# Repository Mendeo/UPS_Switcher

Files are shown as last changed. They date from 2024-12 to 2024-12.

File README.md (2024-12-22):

# Автоматическое выключение и включение домашнего сервера при перебоях с электричеством

Устройство, которое в момент отключения внешнего электричества подаёт сигнал на компьютер, чтобы тот выключился, ожидает его выключения и механически отключает источник бесперебойного питания (ИБП), к которому этот компьютер подключён. После возобновления электроснабжения - снова механически включает бесперебойник.

Состояние электросети отслеживает микроконтроллер в виде Arduino Pro Mini. Когда электричество отключают, то ардуино подаёт сигнал на GPIO контакт. Если в роли компьютера выступает компьютер с GPIO, например Raspberry Pi, то он сразу получает сигнал на выключение. Если это обычный компьютер (без GPIO), то требуется ещё один промежуточный контроллер в виде Arduino Nano, который принимает сигнал от GPIO, а с компьютером связан через USB. Для включения и выключения бесперебойника используется сервомашинка, которая нажимает на кнопку на ИБП. Если электричество вернут в процессе отключения компьютера, то кнопка нажимается дважды, чтобы снова включить компьютер. Ожидая появления электричества, устройство работает от батареек. Скетч для прошивки Arduino Pro Mini - контроллера основного устройства находится в файле [controller/controller.ino](controller/controller.ino). А скетч для Arduino Nano (промежуточный контроллер для компьютеров без GPIO) в файле [comp/serial/controller/controller.ino](comp/serial/controller/controller.ino).

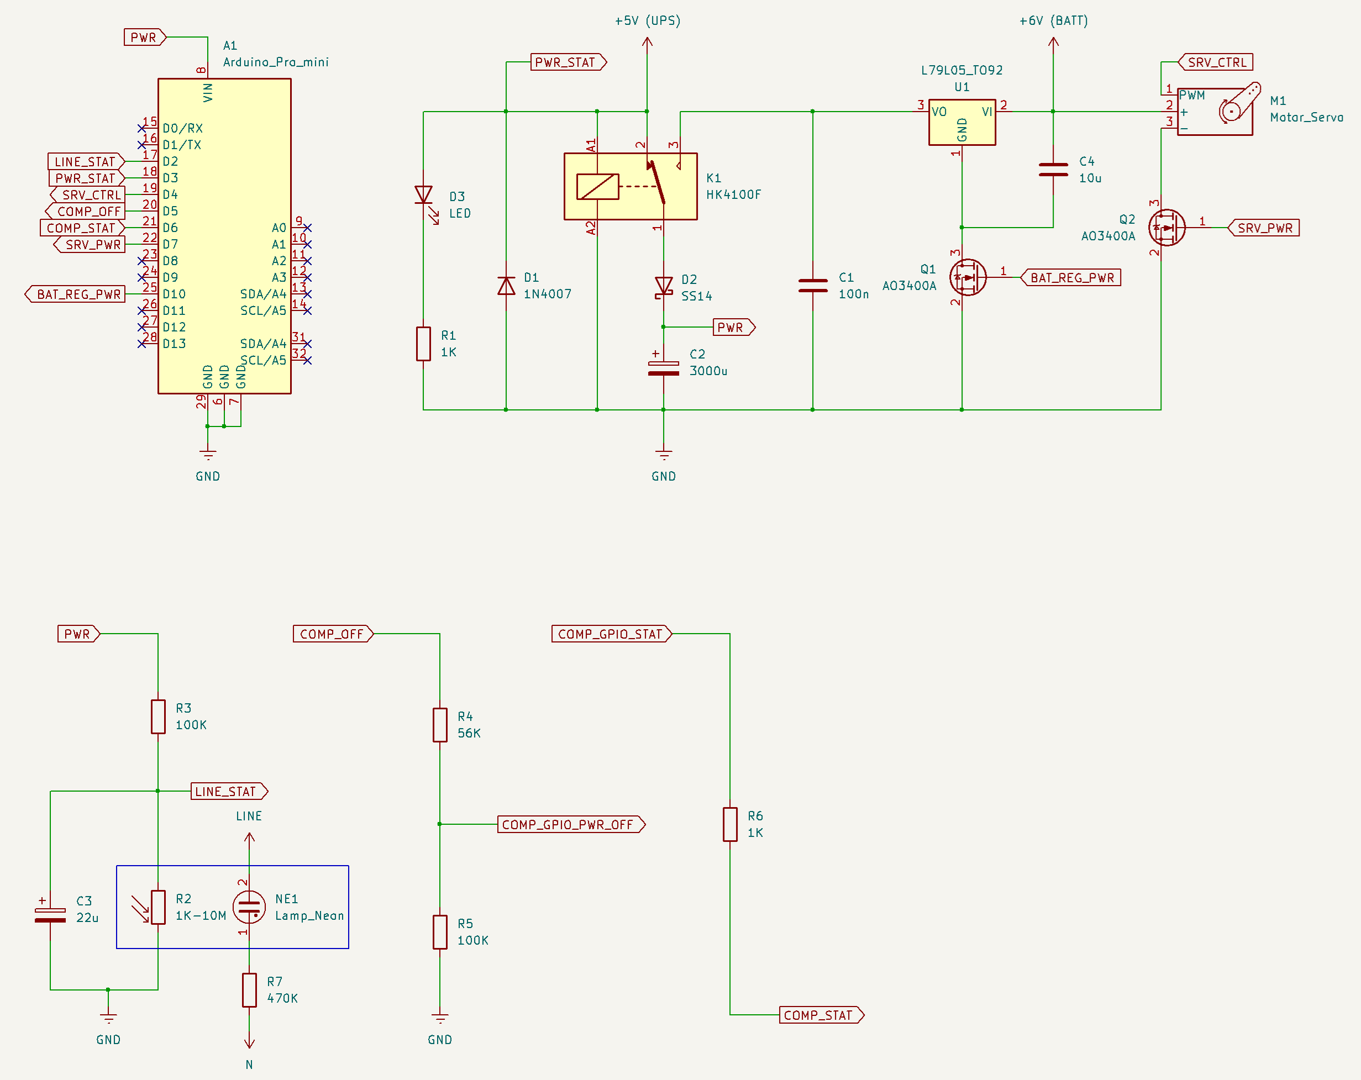
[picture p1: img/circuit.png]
Электрическая схема устройства


Для переключения источника питания устройства применяется пятивольтовое реле. На схеме используется HK4100F, катушка которого потребляет примерно 40 мА. Диод D1 служит для защиты от обратного тока при переключении катушки. При подаче питания на катушку устройство питается от внешнего источника. Катушка сразу подключена к внешнему питанию, поэтому как только оно появляется, то прибор сразу переходит на него.

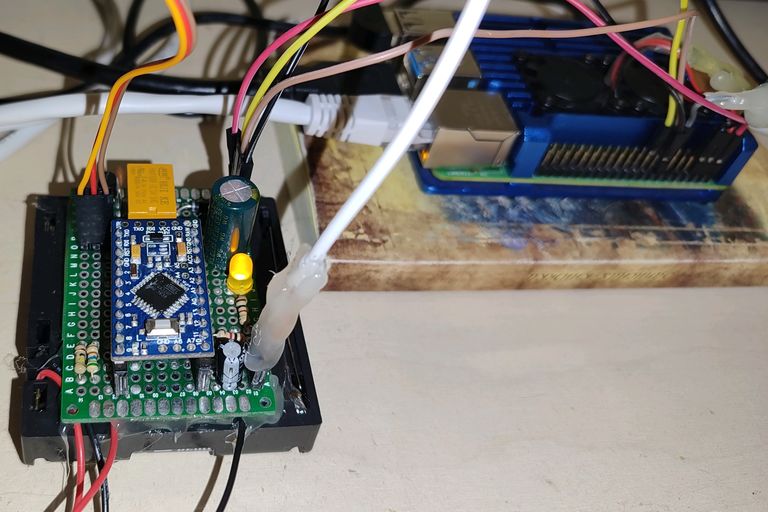
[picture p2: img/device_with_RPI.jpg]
Внешний вид устройства


При отключении питания катушка отключается и реле переключает питание на батарейное. Я использую 4 батарейки AA, что в сумме даёт напряжение 6В, поэтому требуется уменьшить его до 5 вольт. Для этого используется линейный 5В преобразователь L79L05 в корпусе TO92. Этот преобразователь в холостом режиме потребляет примерно 2,5 мА, поэтому будет сажать батарейки даже если устройство питается от внешнего питания. Чтобы этого не было, предусмотрен транзистор Q1, который полностью размыкает цепь связанную с батарейками, когда они не должны использоваться и открывается при переходе на батарейное питание при помощи сигнала от ардуино. О наличии внешнего питания ардуино судит по сигналу PWR_STAT.
Ещё для экономии батареек с Arduino Pro Mini удалены светодиод, который горит при наличии питания и преобразователь напряжения, который в данном проекте не используется, но потребляет ток. Каждый раз при переключении на батарейки микроконтроллер проверяет напряжение питания. И если оно будет ниже допустимого, то выдаст сообщение об ошибке путём моргания оставшегося светодиода (13-й пин). Проверка напряжения реализована путём переключения АЦП микроконтроллера на измерение внутреннего опорного напряжение 1,1 вольта. При этом опорное напряжение самого АЦП остаётся как обычно - напряжение питания. Поэтому результат измерения 1,1 вольта будет зависеть от напряжения питания.

Чтобы ардуинка не выключалась в момент переключения питания предусмотрен конденсатор C2 ёмкостью 3000 мкФ. Но одного конденсатора недостаточно, т.к. из схемы видно, что при отключении внешнего питания, катушка реле продолжит питаться уже от конденсатора и питание быстро не переключится. Чтобы этого избежать установлен диод Шоттки. Он съедает примерно 0,2 вольта входного напряжения, поэтому на ардуино приходит примерно 4,8 вольта.

Сервомашинка питается только от батареек. Чтобы электроника сервомашинки не сажала батарейки в простое, предусмотрен транзистор Q2, который открывается ардуиной только на время её работы. В проекте используется самая распространённая 9-граммовая серва. Она просто приклеивается к ИБП на толстый двухсторонний скотч. Для работы с сервой используется стандартная для ардуино библиотека [Servo](https://reference.arduino.cc/reference/en/libraries/servo/). Для настройки угла поворота, достаточного для нажимания кнопки, я сделал небольшую тестовую прошивку, которую можно залить в удобную для тестрования ардуино (Arduino UNO).

```c++
#define LED 13
#define SERVO_CONTROL 4
#include <Servo.h>

Servo _srv;

void setup()
{
  pinMode(LED, OUTPUT);
  pinMode(SERVO_CONTROL, OUTPUT);
  _srv.attach(SERVO_CONTROL);
  Serial.begin(9600);
  _srv.write(0);
}

int _angle = 0;

void loop()
{
  if (Serial.available())
  {
    _angle = Serial.readString().toInt();
    Serial.println(_angle);
    _srv.write(_angle);
    delay(500);
    _srv.write(0);
  }
}
```

В сериал мониторе нужно вводить градус поворота. Сервомашинка будет на этот угол поворачиваться, а затем возвращаться в нулевое положение. Нужно добиться, чтобы кнопка успешно нажималась и отжималась и сделать на градус два больше для запаса.

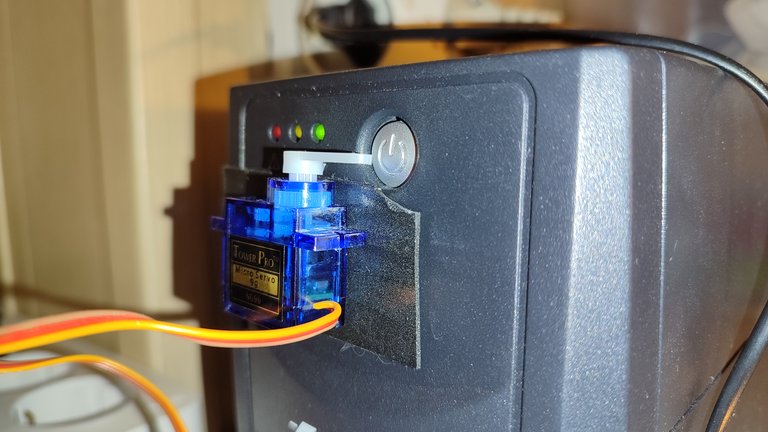
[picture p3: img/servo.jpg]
Сервомашинка, приклеенная к ИБП


Ардуино общается с компьютером или промежуточной Arduino Nano при помощи GPIO. Всего используется два GPIO контакта: COMP_OFF и COMP_STAT.
* COMP_OFF - выходной сигнал Arduino Pro Mini (5-й pin). При высоком уровне на нём компьютер получает сигнал о необходимости выключится. Т.к. мини ПК с GPIO, например, Raspberry Pi использует 3-х вольтовую логику, то COMP_OFF преобразуется во входной сигнал COMP_GPIO_PWR_OFF для Raspberry Pi напряжением чуть меньше 3,3 вольта. Для этого используется делитель, в верхнем плече которого резистор на 56 кОм, а в нижнем - на 100 кОм.
* COMP_STAT - это входной сигнал Arduino Pro Mini (6-й pin) с внутренней подтяжкой к высокому уровню. Когда компьютер включается, он должен установить на этот контакт низкий уровень. Так устройство поймёт, что компьютер работает. COMP_STAT переходит в выходной для GPIO компьютера или промежуточной Arduino Nano контакт COMP_GPIO_STAT. На всякий случай связь сделана через резистор в 1 кОм.

Прибор должен получать информацию о наличии напряжения в розетке. Для этого собирается индикатор напряжения в сети в виде обычной неоновой лампочки NE-2 и фоторезистора. Лампочка питается от сети через резистор 470 кОм. Лампочка и фоторезистор помещаются в пластиковый корпус, изготовленный на 3D принтере. Их выводы помещаются в отдельные корпуса, которые служат для изоляции выводов. Ещё две детали служат для помещения в них подводящих проводов: 230В - к лампе и от прибора к фоторезистору. После сборки отдельные части склеиваются цианокрилатным клеем с содой. Я печатал PETG пластиком. Модели отдельных частей, а также исходный код для среды OpenScad лежат в папке [lineDetector](lineDetector)

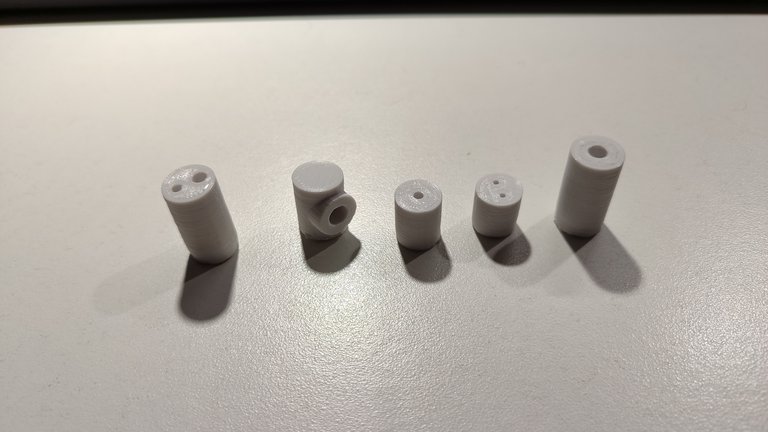
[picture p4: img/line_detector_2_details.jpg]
Детали корпуса индикатора напряжения в сети второй версии


Все оголённые выводы я дополнительно поместил в термоусадку:

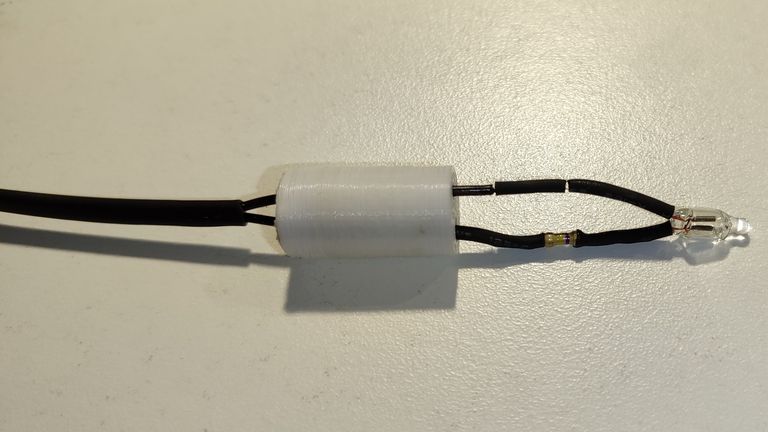
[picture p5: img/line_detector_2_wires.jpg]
Все оголённые выводы дополнительно в термоусадке


Детектор в сборе:

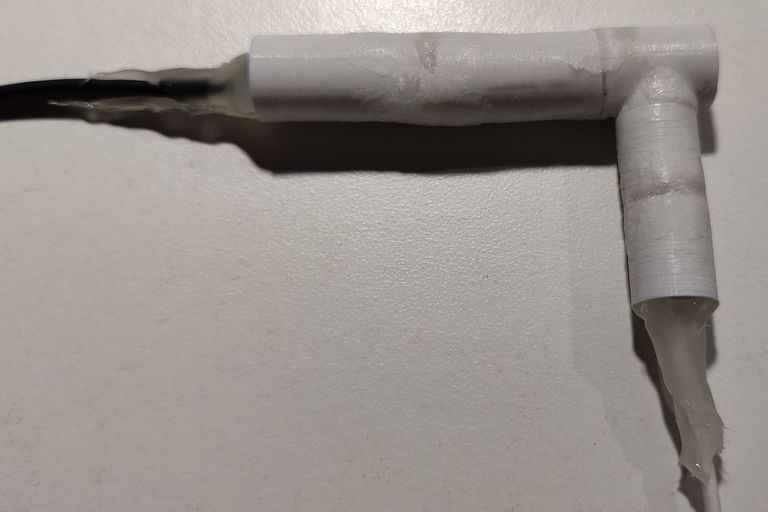
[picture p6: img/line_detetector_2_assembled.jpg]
Индикатор напряжения в сети в распечатанном корпусе


Но какой бы толщины не были стенки, пластик всё равно пропускает свет. Поэтому, чтобы всё работало, нужно обернуть полученное изделие в фольгу. Для этого идеально подходит алюминиевый скотч.

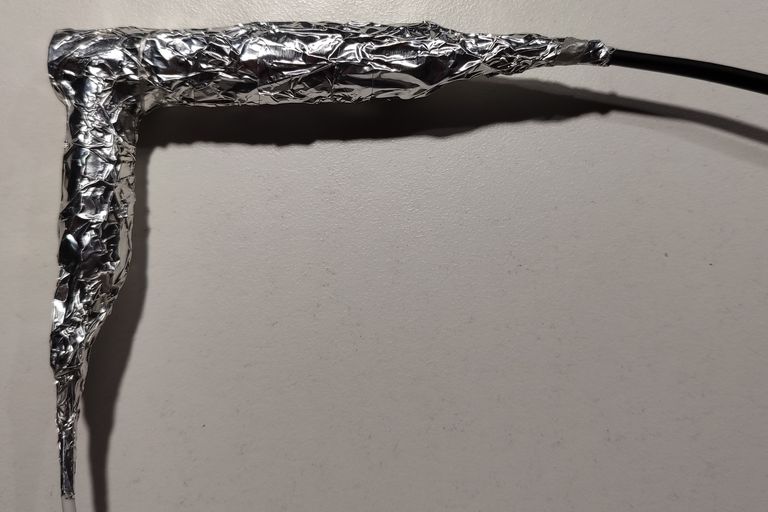
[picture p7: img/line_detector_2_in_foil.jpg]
Индикатор напряжения в сети в распечатанном корпусе и в фольге


В моём случае фоторезистор в полной темноте имеет сопротивление больше 200 МОм, а при освещение неоновой лампочкой - сопростивление падает примерно до 2 кОм. Сигнал LINE_STAT формируется из делителя напряжения, где фоторезистор входит в нижнее плечо. Верхнее плечо - резистор на 100 кОм. В этом случае сигнал LINE_STAT является инверсным: когда электричество есть на нём уровень около нуля, а при отключении сети: почти 5 вольт. Для того, чтобы убрать пульсации и случайные срабатывания ставится конденсатор C3. На схеме указан конденсатор на 22 мкФ. В этом случае детектор срабатывает аж почти через две секунды после отключения электричества в сети. Можно варьировать как удобно.

Программная часть для компьютера написана на языке Tcl. Для компьютеров с GPIO (Raspberry Pi) используется файл [comp/rpi_gpio/watcher.tcl](comp/rpi_gpio/watcher.tcl). В коде задан входным контактом 27-ой пин, выходным - 22-й пин. Управление GPIO в этом коде осуществляется через библиотеку [libgpiod](https://git.kernel.org/pub/scm/libs/libgpiod/libgpiod.git/about/). А именно, используются готовые утилиты для работы с GPIO. Для отслеживания входных сигналов применяется утилита gpiomon, а для установки выходных сигналов - gpioset. Одним из преимуществ такого подхода в управлении GPIO является то, что скрипт watcher.tcl имеет монопольный доступ к GPIO и пока его процесс не завершён, никакой другой процесс не может иметь доступа к используемым watcher.tcl GPIO контактактам, что положительно сказывается на безопасности. Библиотека libgpiod уже предустановлена в последних версиях Raspbian OS, но если нет, то её можно установить.

```
sudo apt install gpiod
```

Для автозагрузки watcher.tcl используется юнит Systemd:

```
[Unit]
Description=Service for communication with the UPS control device

[Service]
User=root
Type=simple
ExecStart=/usr/bin/tclsh /path/to/watcher.tcl

[Install]
WantedBy=multi-user.target
```

Для компьютеров без GPIO, использующих для связи с основным устройством дополнительную Arduino Nano исходный код расположен в файле [comp/serial/comp/watcher.tcl](comp/serial/comp/watcher.tcl). Эта программа в качестве параметра принимает путь к последовательному порту, к которому подключено Arduino Nano (обычно /dev/ttyUSB0). Этот путь следует добавить к ExecStart в юните выше. Алгоритм прост: Arduino Nano всё время шлёт "a\r\n". Когда watcher.tcl запускается и получает с последовательного порта эту команду, то она отсылает "+". Ардуино перестаёт слать "a\r\n" и уходит в глубокий сон (почти перестаёт потреблять энергию). Когда настаёт время выключить сервер, то ардуино просыпается и всё время шлёт "-\r\n".

Если используется Raspberry Pi, то устройство питается от выводов 5 вольт и земля самого одноплатника, т.к. на эти пины питания поступает напряжение даже если Raspberry Pi выключено. В случае обычного компьютера или мини ПК требуется организовать отдельное питание устройства от блока питания, подключённого к ИБП. В моём случае, например, я использовал блок питания самого компьютера с дополнительными выводами, и плату понижения напряжения для преобразования 12 вольт в 5 вольт.

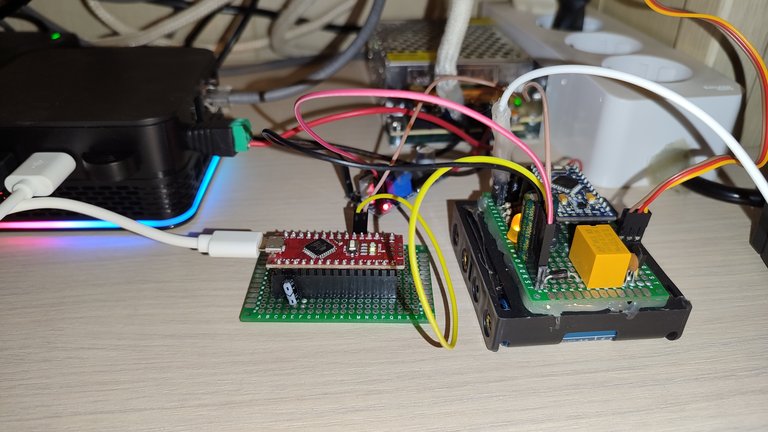
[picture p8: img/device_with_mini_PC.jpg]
Мини ПК с Ардуино вместо GPIO


Итак, для начала работы устройства, нажимаем кнопку reset на ардуино. Если всё нормально, то сначала сервомашинка издаст звук, означающий что устройство включилось и что качалка установлена на нулевой угол. Также, загорится светодиод - обозначающий, что ардуина включилась и пока ещё не ушла в сон. И через некоторое время он погаснет, обозначая, что микроконтроллер ушёл в глубокий сон. Всё. Мониторинг электросети включён. Если же после нажатия reset светодиод начал моргать, то значит нужно искать ошибку. При включении, микроконтроллер проверяет основные сигналы. В случае обнаружения ошибки, ардуино сообщит об этом путём мигания светодиода. Прежде всего устройство должно питаться от основного питания (не батарейки). В противном случае светодиод будет моргать раз в секунду. Эта же ошибка возникнет при сбоях при переключении бесперебойника, если он не включится или не выключится. Далее, проверяется наличие сетевого напряжения. В случае его отсутствия светодиод замигает 10 раз в секунду. Если всё нормально, устройство будет ждать включения сервера (пока не будет притянут к земле соответствующий контакт). Если в течении 3-х минут этого не произойдёт, то светодиод начнёт мигать 2 раза в секунду. И наконец, последняя ошибка - это низкий уровень батареек. Он проверяется при переключении на батарейное питание. В этом случае диод будет мигать 1 раз в 5 секунд. Во всех случаях мигание будет продолжаться 10 минут, потом ардуино уйдёт в сон.

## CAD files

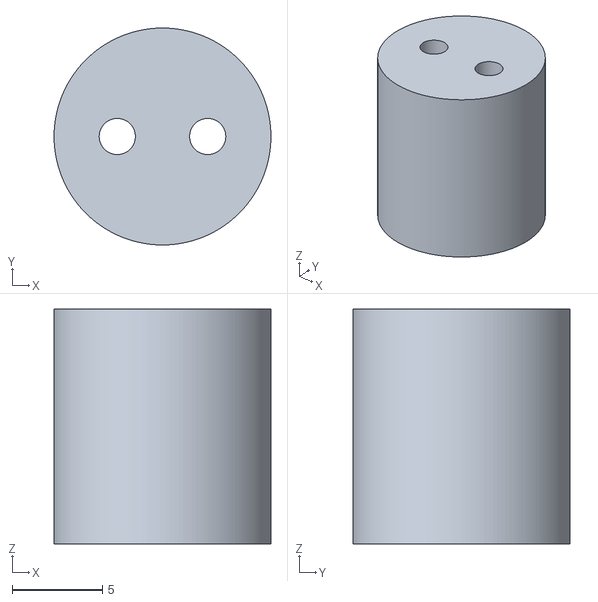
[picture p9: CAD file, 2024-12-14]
lineDetector/resistorPart2.stl
12.0 x 12.0 x 13.0

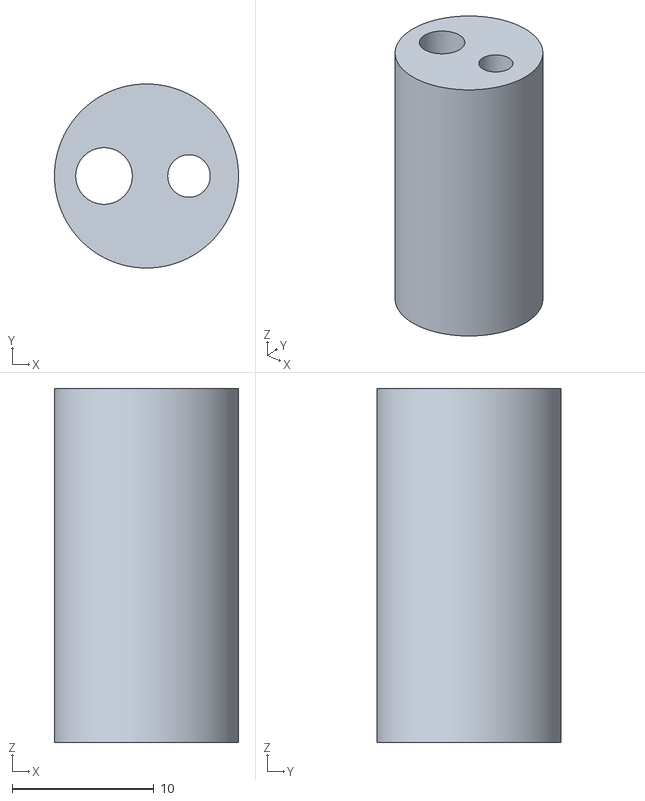
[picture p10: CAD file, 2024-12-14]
lineDetector/lampPart2.stl
13.0 x 13.0 x 25.0

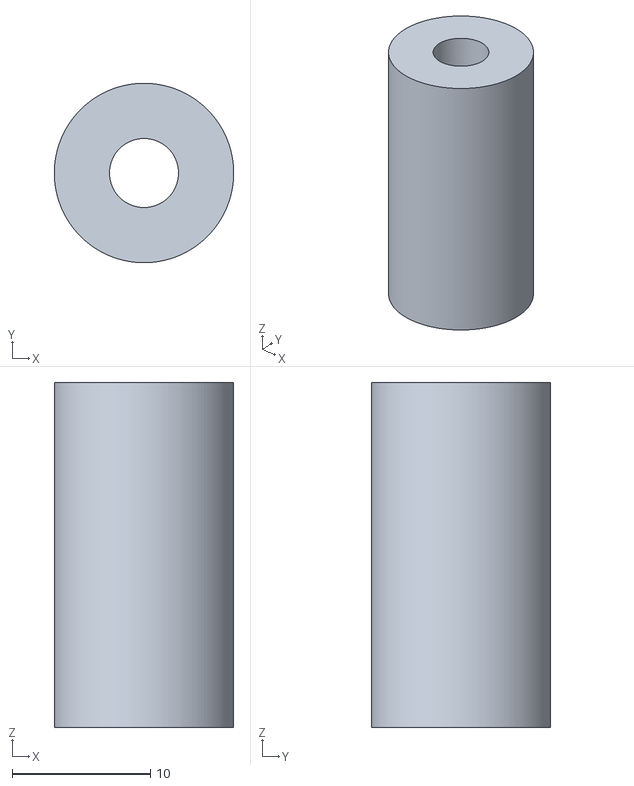
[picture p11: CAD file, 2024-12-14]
lineDetector/lampPart3.stl
13.0 x 13.0 x 25.0

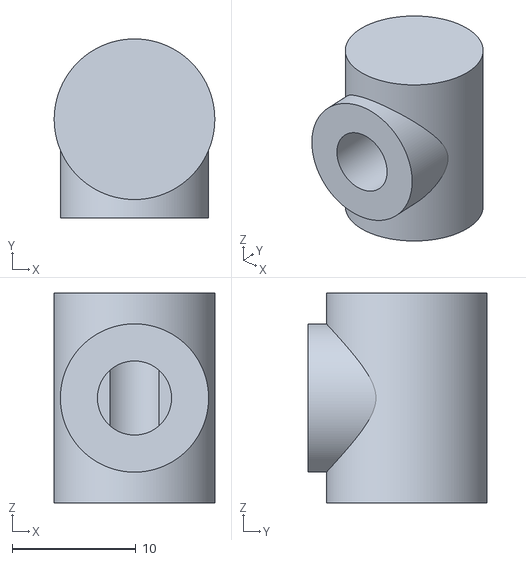
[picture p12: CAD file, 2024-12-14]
lineDetector/lampResistorPart1.stl
13.0 x 14.5 x 17.0

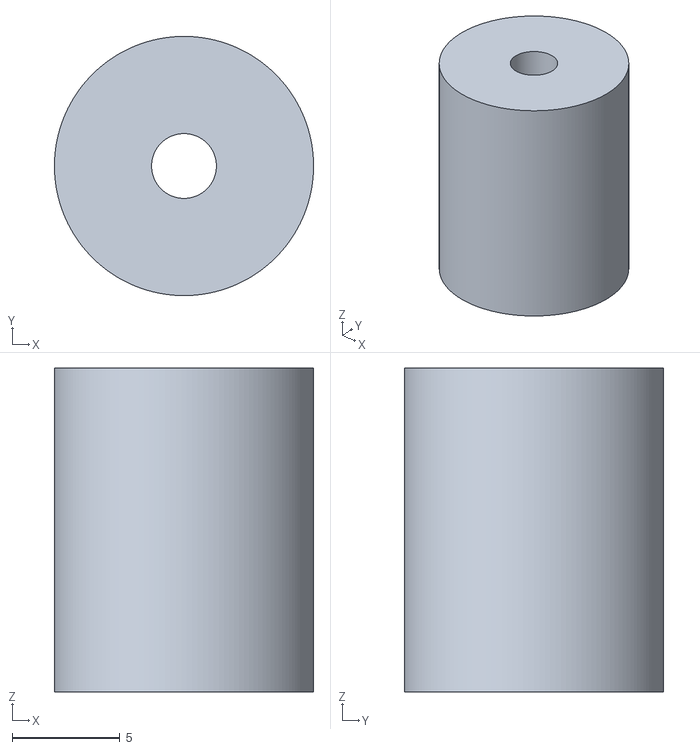
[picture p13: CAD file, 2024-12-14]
lineDetector/resistorPart3.stl
12.0 x 12.0 x 15.0

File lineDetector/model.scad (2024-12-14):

$fn = 150;

lampD = 13;
resistorD = 12;
resistorPart1H = 8;
resistorPart2H = 13;
resistorPart3H = 15;
lampPart1H = 17;
lampPart2H = 25;
lampPart3H = 25;
wireResistorD = 2;
wireLampD = 3;
wireLampWithResistorD = 4;
wireDeltaResistor = 5;
wireDeltaLamp = 6;
wallTLamp = 4;
wallTResistor = 3;
lampCabelD = 5;
resistorCabelD = 3;

/*Отдельно для печати*/
//lampResistorPart1();
lampPart2();
//lampPart3();
//resistorPart2();
//resistorPart3();

/*Общий вид в сборе*/
/*
lampResistorPart1();
%translate([0, 0, -lampPart2H])
lampPart2();
translate([0, 0, -lampPart2H - lampPart3H])
lampPart3();

%translate([0, -resistorPart1H, lampPart1H / 2])
rotate([90, 0, 0])
resistorPart2();
translate([0, -resistorPart1H - resistorPart2H, lampPart1H / 2])
rotate([90, 0, 0])
resistorPart3();
*/

module lampResistorPart1()
{
	translate([0, 0, lampPart1H - wallTLamp])
	cylinder(h = wallTLamp, d = lampD);
	difference()
	{
		union()
		{
			cylinder(h = lampPart1H, d = lampD);
			translate([0, -(lampD / 2 - wallTLamp), lampPart1H / 2])
			rotate([90, 0, 0])
			cylinder(h = resistorPart1H - (lampD / 2 - wallTLamp), d = resistorD);
		}
		translate([0, 0, -1])
		cylinder(h = lampPart1H + 2, d = lampD - 2 * wallTLamp);
		translate([0, -(lampD / 2 - wallTLamp) + 1, lampPart1H / 2])
		rotate([90, 0, 0])
		cylinder(h = resistorPart1H + 1, d = resistorD - 2 * wallTResistor);
	}
}

module resistorPart2()
{
	difference()
	{
		cylinder(h = resistorPart2H, d = resistorD);
		translate([0, 0, -1])
		{
			translate([wireDeltaResistor / 2, 0, 0])
			cylinder(h = lampPart2H + 2, d = wireResistorD);
			translate([-wireDeltaResistor / 2, 0, 0])
			cylinder(h = lampPart2H + 2, d = wireResistorD);
		}
	}
}

module resistorPart3()
{
	difference()
	{
		cylinder(h = resistorPart3H, d = resistorD);
		translate([0, 0, -1])
		cylinder(h = resistorPart3H + 2, d = resistorCabelD);
	}
}

module lampPart2()
{
	difference()
	{
		cylinder(h = lampPart2H, d = lampD);
		translate([0, 0, -1])
		{
			translate([wireDeltaLamp / 2, 0, 0])
			cylinder(h = lampPart2H + 2, d = wireLampD);
			translate([-wireDeltaLamp / 2, 0, 0])
			cylinder(h = lampPart2H + 2, d = wireLampWithResistorD);
		}
	}
}

module lampPart3()
{
	difference()
	{
		cylinder(h = lampPart3H, d = lampD);
		translate([0, 0, -1])
		cylinder(h = lampPart3H + 2, d = lampCabelD);
	}
}

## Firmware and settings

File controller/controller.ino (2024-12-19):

#include <LowPower.h>
#include <Servo.h>

/*
  Сигнал COMP_STATUS инверсный
*/

#define INTERNAL_REF_REAL_VOLTAGE 1.1
#define SERVO_ANGLE 33
#define SERVO_PUSH_TIME 400 //Время на нажатие, зависит от угла.

#define LED 13
#define LINE_STATUS 2
#define BAT_5V_REGULATOR 10
#define SERVO_POWER 7
#define SERVO_CONTROL 4
#define COMP_POWER_OFF_COMMAND 5
#define COMP_STATUS 6
#define MAIN_POWER_STATUS 3

#define COMP_NOT_READY_ERROR 500
#define LOW_BATTERY_ERROR 5000
#define SWITCHING_POWER_ERROR 1000
#define LINE_IS_DOWN_ERROR 100

#define WAIT_COMP_AFTER_START_TIME 180000
#define TIME_FOR_COMP_POWEROFF_AFTER_LINE_DOWN 30000
#define TIME_FOR_UPS_POWEROFF_AFTER_COMP 43000
#define TIME_BEFORE_COMP_POWERON 20000
#define TIME_BEFORE_DEEP_SLEEP 10000

#define BLINK_ERROR_TIME 600000

unsigned long _eventTime = 0;
bool _compIsOn = true;
bool _isMainPower = true;
Servo _srv;
bool _lineIsOk = true;
bool _needSleep = false;
volatile bool _needCheckLine = true;

void setup()
{
  pinMode(LINE_STATUS, INPUT);
  pinMode(MAIN_POWER_STATUS, INPUT);
  pinMode(COMP_STATUS, INPUT_PULLUP);

  pinMode(LED, OUTPUT);
  pinMode(SERVO_POWER, OUTPUT);
  pinMode(COMP_POWER_OFF_COMMAND, OUTPUT);
  pinMode(BAT_5V_REGULATOR, OUTPUT);

  digitalWrite(LED, HIGH);
  digitalWrite(BAT_5V_REGULATOR, HIGH);

  rotateServo(0);
  compPowerOn();
  if (!digitalRead(MAIN_POWER_STATUS)) blink(SWITCHING_POWER_ERROR);
  digitalWrite(BAT_5V_REGULATOR, LOW);
  prepareADCForVCCmeasuring();
  delay(3000); //На зарядку конденсатора перед первой проверкой линии
  checkLine();
  if (!_lineIsOk) blink(LINE_IS_DOWN_ERROR);

  unsigned long timer = millis();
  while (digitalRead(COMP_STATUS))
  {
    if (millis() - timer >= WAIT_COMP_AFTER_START_TIME)
    {
      blink(COMP_NOT_READY_ERROR);
    }
  }
}

void onLineChange()
{
  _needCheckLine = true;
}

void loop()
{
  if (_isMainPower && _compIsOn && _lineIsOk && (millis() - _eventTime) >= TIME_BEFORE_DEEP_SLEEP && !_needCheckLine)
  {
    _needSleep = true;
  }
  else if (_isMainPower && _compIsOn && !_lineIsOk && (millis() - _eventTime) >= TIME_FOR_COMP_POWEROFF_AFTER_LINE_DOWN  && !_needCheckLine)
  {
    compPowerOff();
    waitForCompPowerOff();
    _eventTime = millis();
  }
  else if (_isMainPower && !_compIsOn && !_lineIsOk && (millis() - _eventTime) >= TIME_FOR_UPS_POWEROFF_AFTER_COMP && !_needCheckLine)
  {
    switchUPS();
    _needSleep = true;
  }
  else if (!_isMainPower && !_compIsOn && _lineIsOk && (millis() - _eventTime) >= TIME_BEFORE_COMP_POWERON && !_needCheckLine)
  {
    switchUPS();
    waitForCompPowerOn();
    _needSleep = true;
  }
  else if (!_isMainPower && !_compIsOn && !_lineIsOk && (millis() - _eventTime) >= TIME_BEFORE_DEEP_SLEEP && !_needCheckLine)
  {
    _needSleep = true;
  }
  else if (_isMainPower && !_compIsOn && _lineIsOk && (millis() - _eventTime) >= TIME_BEFORE_COMP_POWERON && !_needCheckLine)
  {
    switchUPS();
    delay(3000);
    switchUPS();
    waitForCompPowerOn();
    _needSleep = true;
  }
  else if (!_isMainPower && _compIsOn && !_needCheckLine)
  {
    _compIsOn = false;
  }
  checkLine();
  if (_needSleep)
  {
    _needSleep = false;
    sleep();
  }
}

void compPowerOff()
{
  digitalWrite(COMP_POWER_OFF_COMMAND, HIGH);
}

void compPowerOn()
{
  digitalWrite(COMP_POWER_OFF_COMMAND, LOW);
}

void rotateServo(int angle)
{
  pinMode(SERVO_CONTROL, OUTPUT);
  digitalWrite(SERVO_POWER, HIGH);
  delay(3);
  _srv.attach(SERVO_CONTROL);
  _srv.write(angle);
  delay(SERVO_PUSH_TIME);
  if (angle > 0)
  {
    _srv.write(0);
    delay(SERVO_PUSH_TIME);
  }
  _srv.detach();
  digitalWrite(SERVO_POWER, LOW);
  pinMode(SERVO_CONTROL, INPUT);
}

void switchUPS()
{
  _isMainPower = digitalRead(MAIN_POWER_STATUS);
  if (_isMainPower) digitalWrite(BAT_5V_REGULATOR, HIGH);
  rotateServo(SERVO_ANGLE);
  unsigned long time = millis();
  while (_isMainPower == digitalRead(MAIN_POWER_STATUS))
  {
    if (millis() - time > 7000) //Основное питание с ардуины должно пропасть или появится не позже, чем через 7 секунд.
    {
      if (_isMainPower) digitalWrite(BAT_5V_REGULATOR, LOW);
      blink(SWITCHING_POWER_ERROR);
    }
  }
  _isMainPower = !_isMainPower;
  if (_isMainPower)
  {
    digitalWrite(BAT_5V_REGULATOR, LOW);
  }
  else
  {
    delay(3000); //На восстановление напряжения.
    float VCC = getVCC();
    if (VCC < 4.1)
    {
      blink(LOW_BATTERY_ERROR);
    }
  }
}

void sleep()
{
  digitalWrite(LED, LOW);
  LowPower.powerDown(SLEEP_FOREVER, ADC_OFF, BOD_OFF);
}

void waitForCompPowerOff()
{
  while (!digitalRead(COMP_STATUS)) {}
  compPowerOn();
  _compIsOn = false;
}

void waitForCompPowerOn()
{
  while (digitalRead(COMP_STATUS)) {}
  _compIsOn = true;
}

void attachInterruptToLineDown()
{
  attachInterrupt(digitalPinToInterrupt(LINE_STATUS), onLineChange, HIGH);
}
void attachInterruptToLineUp()
{
  attachInterrupt(digitalPinToInterrupt(LINE_STATUS), onLineChange, LOW);
}

void checkLine()
{
  if (_needCheckLine)
  {
    _needCheckLine = false;
    detachInterrupt(digitalPinToInterrupt(LINE_STATUS));
    delay(50);
    digitalWrite(LED, HIGH);
    bool currentValue = !digitalRead(LINE_STATUS);
    if (currentValue != _lineIsOk)
    {
      _lineIsOk = currentValue;
      _eventTime = millis();
      _needSleep = false;
    }
    if (_lineIsOk)
    {
      attachInterruptToLineDown();
    }
    else
    {
      attachInterruptToLineUp();
    }
  }
}

void blink(int period)
{
  digitalWrite(LED, HIGH);
  delay(period);
  unsigned long timer = millis();
  while (true)
  {
    digitalWrite(LED, LOW);
    delay(period);
    digitalWrite(LED, HIGH);
    delay(period);
    if (millis() - timer >= BLINK_ERROR_TIME) sleep();
  }
}

void prepareADCForVCCmeasuring()
{
  /*
    Настройка АЦП на считывание значения из внутреннего ИОН. При этом опорное напряжение - это напряжение питания.
    REFS1 = 0 и REFS0 = 1 - означает, что опорное напряжение - это напряжения питания. (стр. 217 datasheet)
    MUX[3..0] = 1110 - Подключает мультиплексор к внутреннему опорнику 1.1В. (стр. 218 datasheet)
    ADLAR = 0 - Означает, что первые 8 бит будут в ADCL и ещё 2 бита - в ADCH (стр. 219 datasheet)
  */
  ADMUX |= (0 << REFS1) | (1 << REFS0) | (1 << MUX3) | (1 << MUX2) | (1 << MUX1) | (0 << MUX0) | (0 << ADLAR);
  ADCSRA |= (0 << ADEN) | (0 << ADATE);; //Пока выключаем АЦП. (ADATE = 0 - выключает постоянное считывание значение по триггеру)
}

void turnOnADC()
{
  ADCSRA |= (1 << ADEN); //Включили АЦП.
}

void turnOffADC()
{
  ADCSRA |= (0 << ADEN); //Выключили АЦП.
}

float getVCC()
{
  turnOnADC();
  delay(20);
  float VCC = getVCC_common();
  turnOffADC();
  return VCC;
}

float getVCC_common()
{
  int n = 3; //Количество преобразований.
  int ADC_sum = 0;
  for (int i = 0; i < n; i++)
  {
    ADCSRA |= (1 << ADSC) ;  //Начали преобразование. 
    while (ADCSRA & (1 << ADSC)) {} //Ждём пока не закончится преобразование (тогда ADSC снова станет нулём)
    ADC_sum += ADC;
  }
  return INTERNAL_REF_REAL_VOLTAGE * 1023.0 / ((float)ADC_sum / (float)n);
}

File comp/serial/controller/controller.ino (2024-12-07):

#include <LowPower.h>

#define LED 13
#define COMP_POWER_OFF_COMMAND 2
#define COMP_STATUS 3
#define SEND_PERIOD 700
#define WAIT_COMP_AFTER_START_TIME 180000
#define WAIT_COMP_ERROR 1000
#define COMP_OFF_COMMAND_AFTER_START_ERROR 500
#define BLINK_ERROR_TIME 600000

unsigned long _timer;
bool _receivePowerOffSignal = false;
bool _needSleep = false;
bool _afterHighEvent = false;
bool _afterLowEvent = true;
volatile bool _ifInterruptIsAttached = false;

/*
  Сигнал COMP_STATUS инверсный
*/

void setup()
{
  pinMode(COMP_POWER_OFF_COMMAND, INPUT);
  pinMode(COMP_STATUS, OUTPUT);
  pinMode(LED, OUTPUT);
  Serial.begin(9600);
  digitalWrite(COMP_STATUS, HIGH);

  if (digitalRead(COMP_POWER_OFF_COMMAND)) blink(COMP_OFF_COMMAND_AFTER_START_ERROR);

  unsigned long timerForSend = millis();
  unsigned long timerForWait = millis();
  while (true)
  {
    if (millis() - timerForSend >= SEND_PERIOD)
    {
      Serial.println('a');
      timerForSend = millis();
    }
    if (Serial.available())
    {
      if (Serial.read() == '+')
      {
        digitalWrite(COMP_STATUS, LOW);
        _timer = millis();
        break;
      }
    }
    if (millis() - timerForWait >= WAIT_COMP_AFTER_START_TIME)
    {
      blink(WAIT_COMP_ERROR);
    }
  }
  _timer = millis();
}

void onCompPowerOffCommand()
{

}

void loop()
{
  if (_ifInterruptIsAttached) detachInterrupt(digitalPinToInterrupt(COMP_POWER_OFF_COMMAND));
  if (_receivePowerOffSignal)
  {
    if (millis() - _timer >= SEND_PERIOD)
    {
      Serial.println('-');
      _timer = millis();
    }
  }
  else
  {
    if (digitalRead(COMP_POWER_OFF_COMMAND))
    {
      if (_afterLowEvent)
      {
        _afterLowEvent = false;
        _afterHighEvent = true;
        _timer = millis();
      }
      if ((millis() - _timer) >= 100)
      {
        _receivePowerOffSignal = true;
        _timer = millis() + SEND_PERIOD;
      }
    }
    else
    {
      if (_afterHighEvent)
      {
        _afterHighEvent = false;
        _afterLowEvent = true;
        _timer = millis();
      }
      if (!_ifInterruptIsAttached && (millis() - _timer) >= 100)
      {
        attachInterrupt(digitalPinToInterrupt(COMP_POWER_OFF_COMMAND), onCompPowerOffCommand, HIGH);
        _ifInterruptIsAttached = true;
        sleep();
      }
    }
  }
}

void sleep()
{
  digitalWrite(LED, LOW);
  LowPower.powerDown(SLEEP_FOREVER, ADC_OFF, BOD_OFF);
}

void blink(int period)
{
  digitalWrite(LED, HIGH);
  delay(period);
  unsigned long timer = millis();
  while (true)
  {
    digitalWrite(LED, LOW);
    delay(period);
    digitalWrite(LED, HIGH);
    delay(period);
    if (millis() - timer >= BLINK_ERROR_TIME) sleep();
  }
}

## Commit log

2024-10-16 Первый коммит
2024-10-16 Добавил протеус
2024-10-17 Добавил измерение напряжения питания
2024-10-17 Нстройка логики работы.
2024-10-20 Улучшил переключение питания. Теперь ждём, пока упадёт напряжение
2024-10-21 Исправление под последнюю версию платы
2024-10-21 Вынес задание реального напряжения внутреннего ИОН в #define
2024-10-21 Удалил Протеус. Исправил название файла для контроллера.
    [controller.ino]
2024-10-21 Сделал код для серверной части
2024-10-23 Добавил включение 5-вольтового регулятора перед подключением питания от батареек, и отключение его при переходе на сетевое питание.
2024-10-23 Улучшил читабельность при вызове getVCC.
2024-10-23 Перешёл на табы.
2024-10-23 Снова перешёл на прообелы, пока Arduino IDE не поддерживает табы.
2024-11-05 Начал работу над управление через последовательный порт.
2024-11-05 Дорабатываю скрипт на tcl
2024-11-06 Добавил код работы с портом на C#
2024-11-06 Переместил дотнетовский файл куда ему надо быть.
2024-11-07 Верунул sln в корень.
2024-11-07 Небольшие исправления в c# коде
2024-11-09 Отладил код ардуино
2024-11-09 Заработал с LowPower
2024-11-10 Ещё немного улучшений
2024-11-10 Удалил лишние файлы (serial на c#). Некоторые переименования.
2024-11-10 Подготовка настроек к эксплуатации.
2024-11-11 Небольшие правки, а также код для ардуино для работы с компом по последовательному порту
2024-11-11 Учёт того, что номер GPIO может начинаться не с нуля
2024-11-11 Добавил подтяжку на вход о статусе компьютера. Тперь этот вход инверсный. Сделал соответствующие исправления.
    [controller.ino]
2024-11-11 Исправления компа с учётом инверсного статустного пина. Добавил комментарий, описывающий смещение номеров GPIO.
    [app.js]
2024-11-11 Добавил консольного вывода.
2024-11-11 Настроил GPIO_SHIFT на работу с Ubuntu
2024-11-11 Исправления по результатам испытаний
    [controller.ino]
2024-11-13 Настроил угол поворота и время поворота.
2024-11-14 Добавил электрическую схему.
    [UPS_Switcher.kicad_sch]
2024-11-14 Добавил код, отвечающий за поиск смещения GPIO. Добавил конфигурацию ESLint.
2024-11-14 Изменил название переменной.
2024-11-14 Исправление опечатки
2024-11-14 Работа над скриптом в tcl.
2024-11-15 Реализовал реагирование на входной сигнал с учётом дребезга. Сделал корректное завершение утилит gpiod.
2024-11-15 Убрал загрушку
2024-11-15 Изменил время ожидания после получения сигнала выключения.
2024-11-15 Удалил лишние файлы. Организовал структуру.
2024-11-15 Добавил вывода в консоль.
2024-11-15 Добавил возможность дописать аргументы к команде выключения компьютера.
2024-11-15 Переделал на инверсный сигнал о том, что компьютер надо выключить.
2024-11-15 Переделал на инверсные сигналы с учётом подтяжки.
2024-11-15 Переделал скрипт с учётом того, что формат вывода gpiomon можно менять, в частности выдавать напрямую числа 0 или 1.
2024-11-15 Небольшие испраления в программе для компа для последовательного порта.
2024-11-15 Улучшение консольного вывода: теперь не выводит пустые строки после успешного завершения программ gpiomon и gpioset.
2024-11-15 Убрал инверсный сигнал и подтяжку для COMP_POWER_OFF. Так как подтяжка уже есть на делителе в приборе.
2024-11-15 Вернул js код
2024-11-15 Испарвления в работе мониторинга на компьютере.
2024-11-16 Сделал завершение программы при возникновении ошибок в gpioset или gpiomon. Выводится сообщение, о том, что произошла ошибка.
2024-11-18 Начал писать сендер в телеграм.
2024-11-18 Добавил шебанг
2024-11-18 Стал делать успешные https запросы.
2024-11-19 Закончил скрипт отправки сообщений в телеграм.
2024-11-19 Небольшие улучшения кода.
2024-11-19 Обновление .gitignore
2024-11-19 Переименование основоного tcl файла.
2024-11-19 Работа над отправкой сообщений из внешнего кода.
2024-11-19 Исправление работы sender.tcl из внешнего скрипта. Добавление в watcher отправки сообщения в телеграм.
2024-11-19 Переделал шебанг
2024-11-19 Исправление ошибок
2024-11-20 Убрал отправку сообщений в телеграм по умолчанию.
2024-11-20 Убрал telegram-sender.
2024-11-23 Улучшил работу мониторинга по сериал порту.
2024-11-23 Удалил ненужное из функции blink.
2024-11-23 Переименование файла.
2024-11-30 Небольшие исправления на схеме.
    [UPS_Switcher.kicad_sch]
2024-11-30 Убрал не нужную константу.
2024-11-30 Отладка прошивки ардуино для сериал порта.
2024-11-30 Улучшение кода.
2024-11-30 Отладка модулей для работы через ком порт.
2024-12-07 Небольшие исправления по таймингам. И основной модуль теперь ждёт включение компа, а не выдаёт сразу ошибку.
    [controller.ino]
2024-12-07 Добавил недостающий конденсатор.
    [UPS_Switcher.kicad_sch]
2024-12-11 Сделал модель для корпуса детектора сети. Пока с произвольными размерами.
    [model.scad]
2024-12-14 Доработал модель по фактическим размерам. Добавил части, скрывающие сам кабель.
    [model.scad]
2024-12-14 Переключил на общий вид модели.
    [model.scad]
2024-12-14 Добавил stl модели.
    [lampPart2.stl, lampPart3.stl, lampResistorPart1.stl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]
2024-12-14 Сгенерировал G-код.
2024-12-14 Изменил диаметр кабеля для лампы.
    [lampPart3.stl, model.scad]
2024-12-14 Обновил температуру стола.
2024-12-14 Изменил некоторые размеры под проводку.
    [lampPart2.stl, model.scad, resistorPart2.stl]
2024-12-19 Увеличил время ожидания переключения питания. Из-за мощных кондёров в блоке питания оно может быть достаточно долгим.
2024-12-22 Небольшие правки схемы
    [UPS_Switcher.kicad_sch]
2024-12-22 Написал README.md
2024-12-22 Удалил g-code из репозитория.
2024-12-22 Исправление опечаток.
2024-12-28 Добавил расчёт выделяемой мощности на резисторе
    [NE-2.ods]
